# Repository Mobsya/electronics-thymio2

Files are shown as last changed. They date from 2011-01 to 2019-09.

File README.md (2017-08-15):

# electronics-thymio2

This is the official [Thymio II](www.thymio.org) electronis repository.
You will find here all files necessary to build and make the main PCB of Thymio II robots.
Source files are in Altium format but you can also found in /outbput common fabrication files. 

Thymio II is an open hardware robot, with its design freely available under a [Creative Commons Attribution-ShareAlike 3.0](https://creativecommons.org/licenses/by-sa/3.0/) license.

## Authors

The current version of the Thymio II robot, is an evolution of a first Thymio robot. 
Both were developed in the context of a collaboration between the [MOBOTS](http://mobots.epfl.ch/) group of the Swiss Federal Institute of Technology in Lausanne ([EPFL](www.epfl.ch)) and the Lausanne Arts School ([ECAL](http://www.ecal.ch)).
For Thymio II, the development was supported by the [NCCR](https://www.nccr-robotics.ch/) Robotics research program, while [Mobsya association](www.mobsya.org) took part in the development and manages the production.

Initial electronics version was made by:
* Dr Fanny Riedo
* Dr Michael Bonani
* Dr Philippe Rétornaz

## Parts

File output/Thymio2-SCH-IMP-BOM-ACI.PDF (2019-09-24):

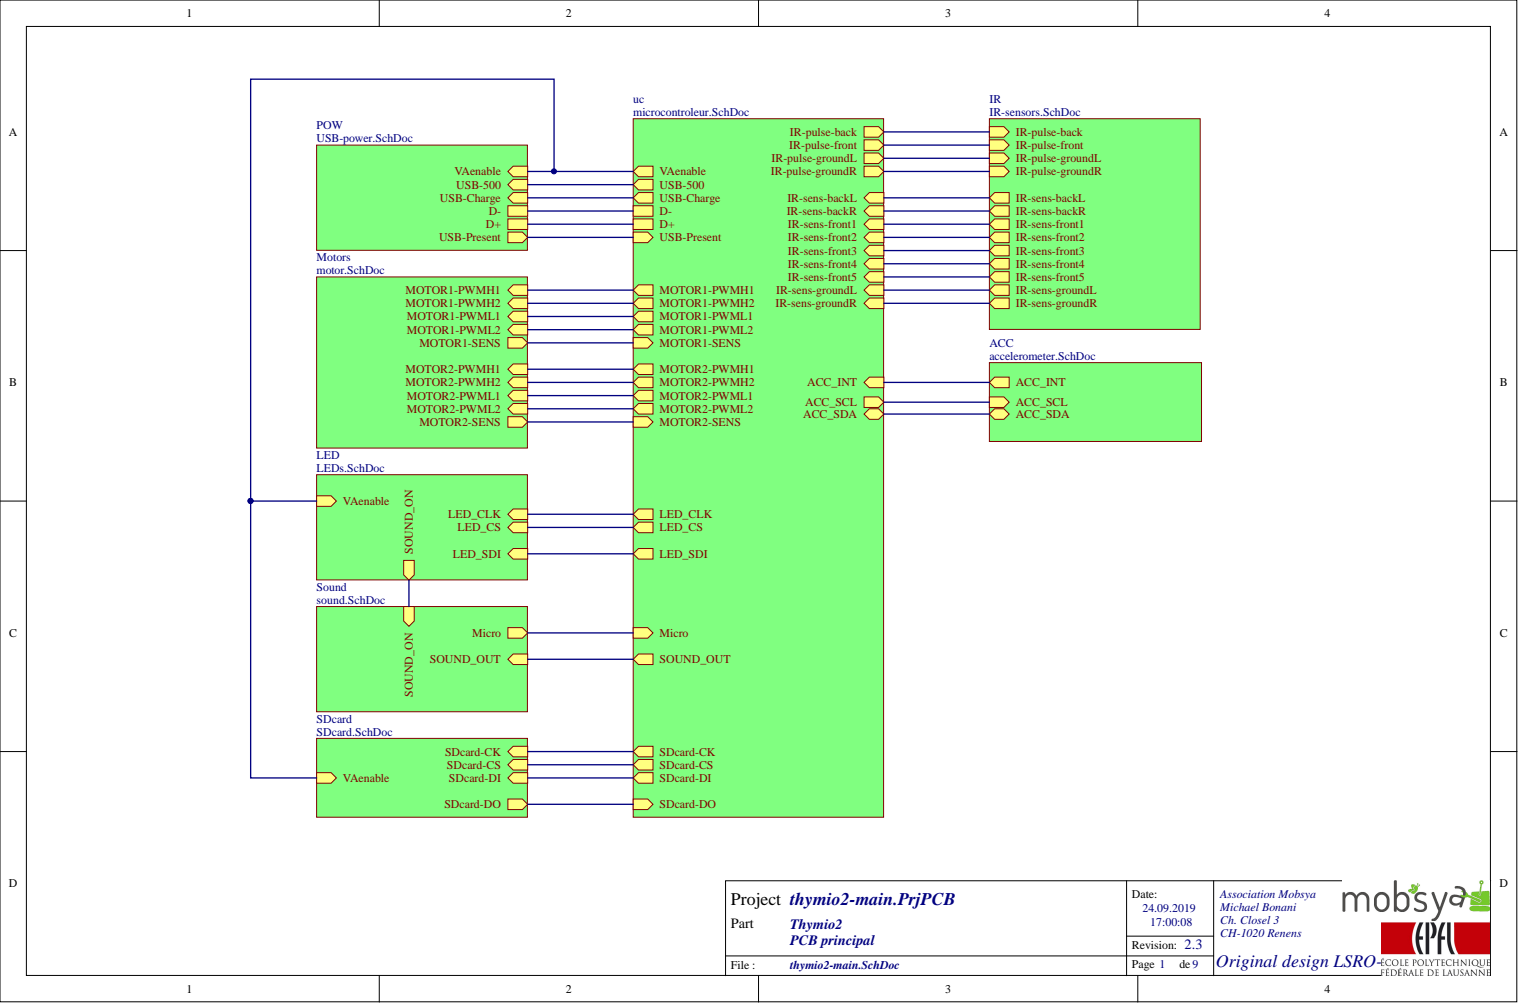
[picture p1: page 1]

S2 | | | | ENVREG 57 | PGC Buton2 2

VCAP/VDDCORE 56 | Buton3 3

Buton4 | | 4

VBUS 34 | | Buton5 | | 5
VUSB 35 | | | | 6

RT1 | USB-500 USB-Charge

R137 | PMA9/RP10/SDA2/CN17/RF4 31

MOTOR1-PWML1 | PMA8/RP17/SCL2/CN18/RF5 32 D-/RG3 36 D+/RG2 37

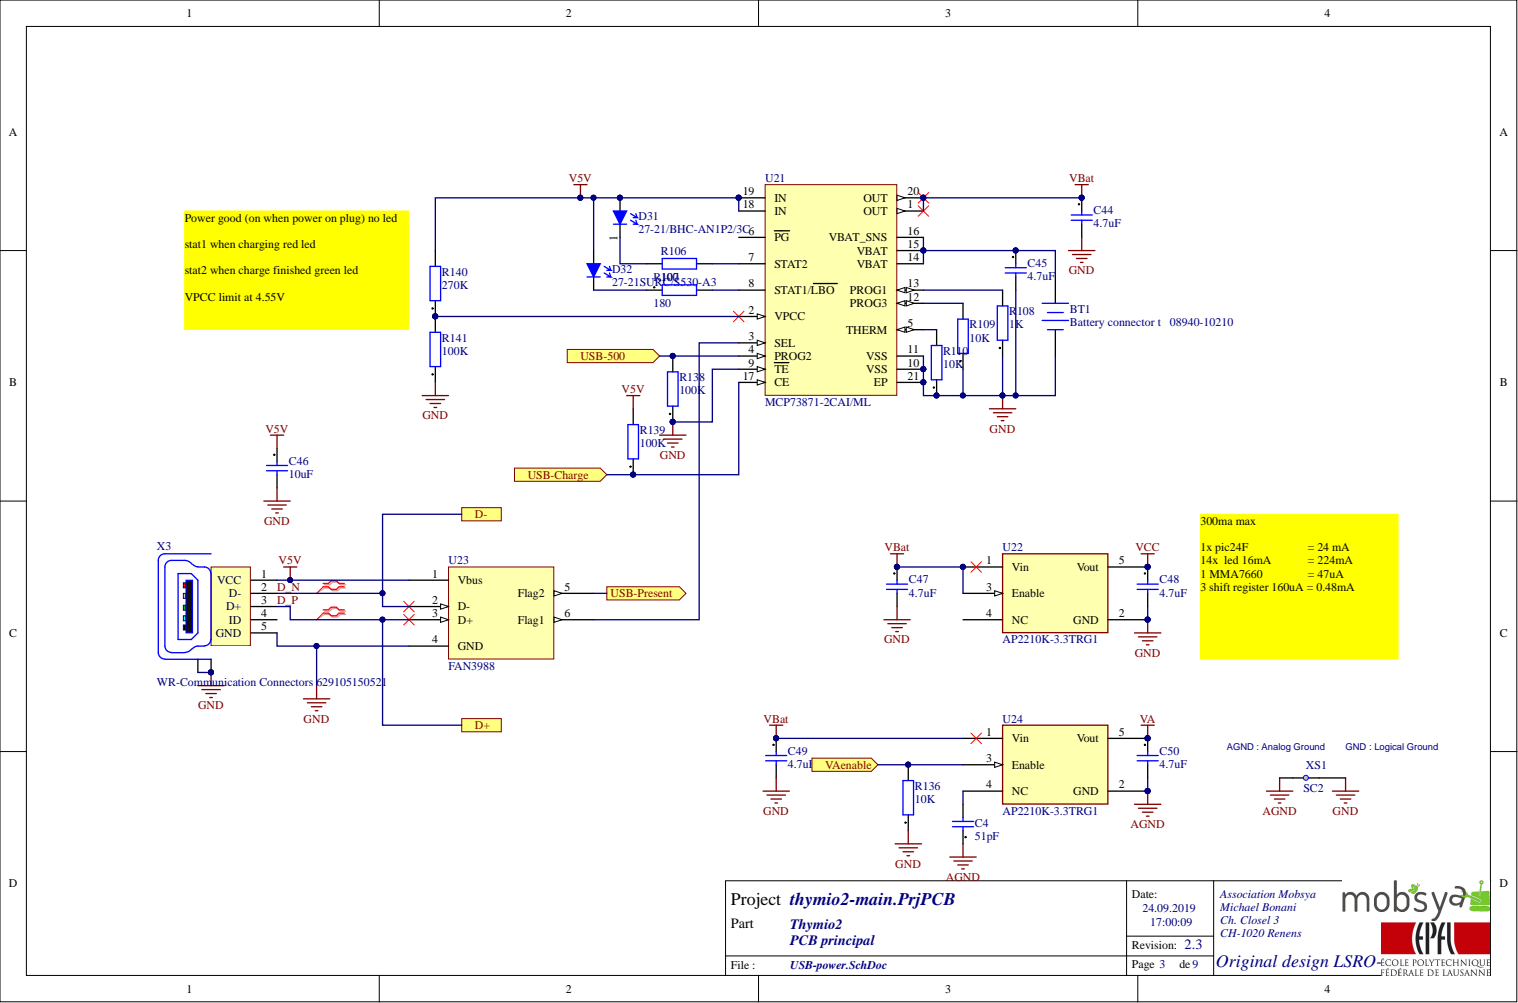
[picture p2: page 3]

Power good (on when power on plug) no led

stat1 when charging red led

stat2 when charge finished green led

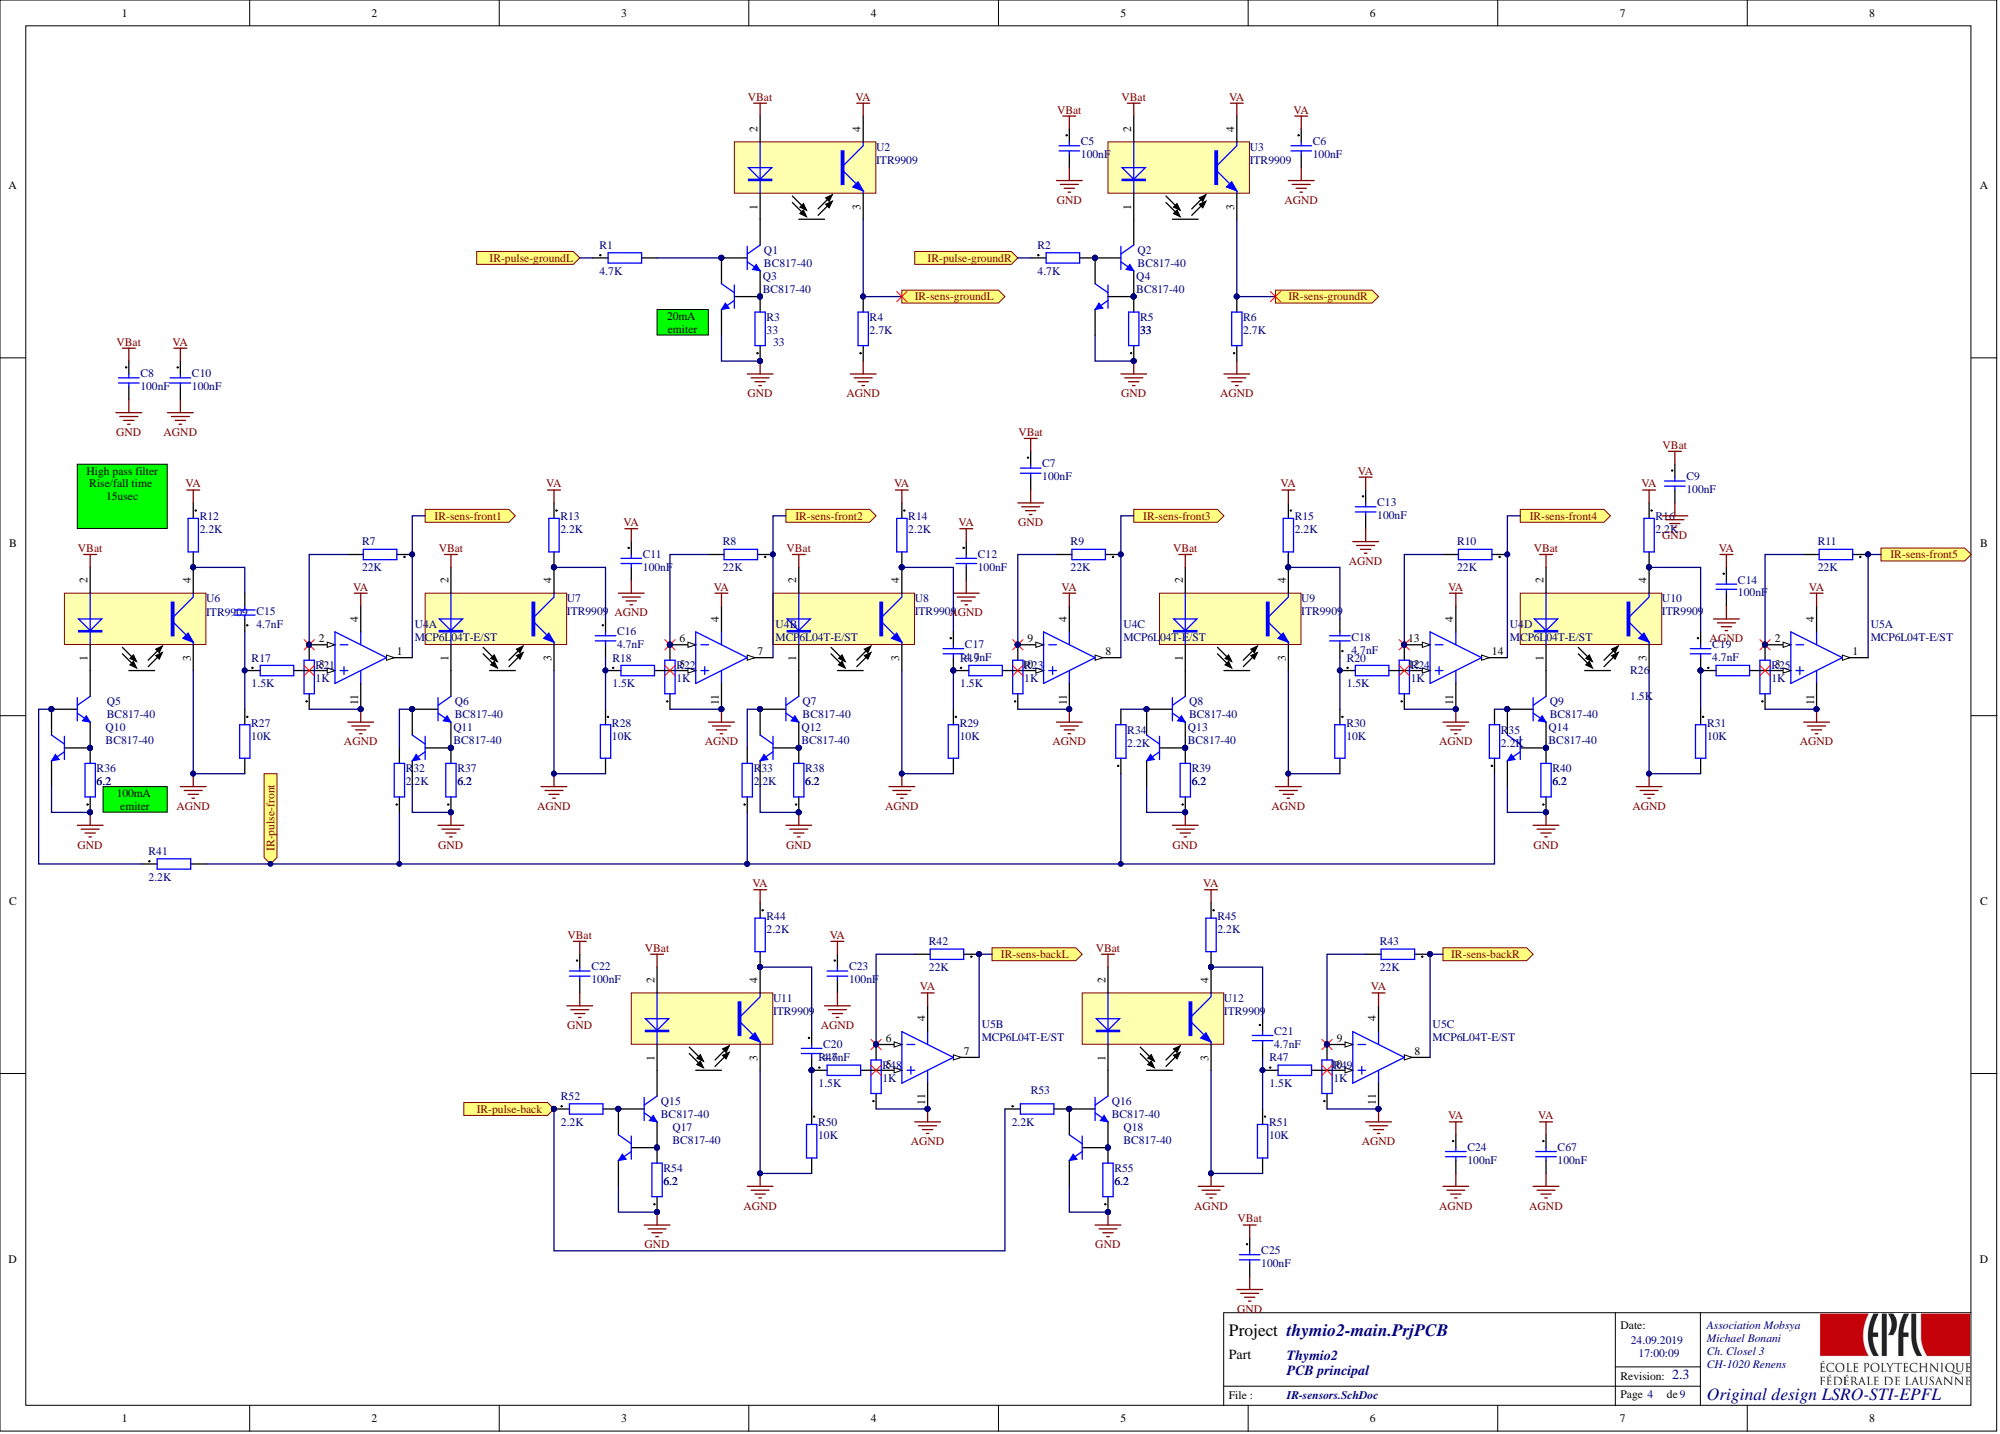
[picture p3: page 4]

100mA emiter

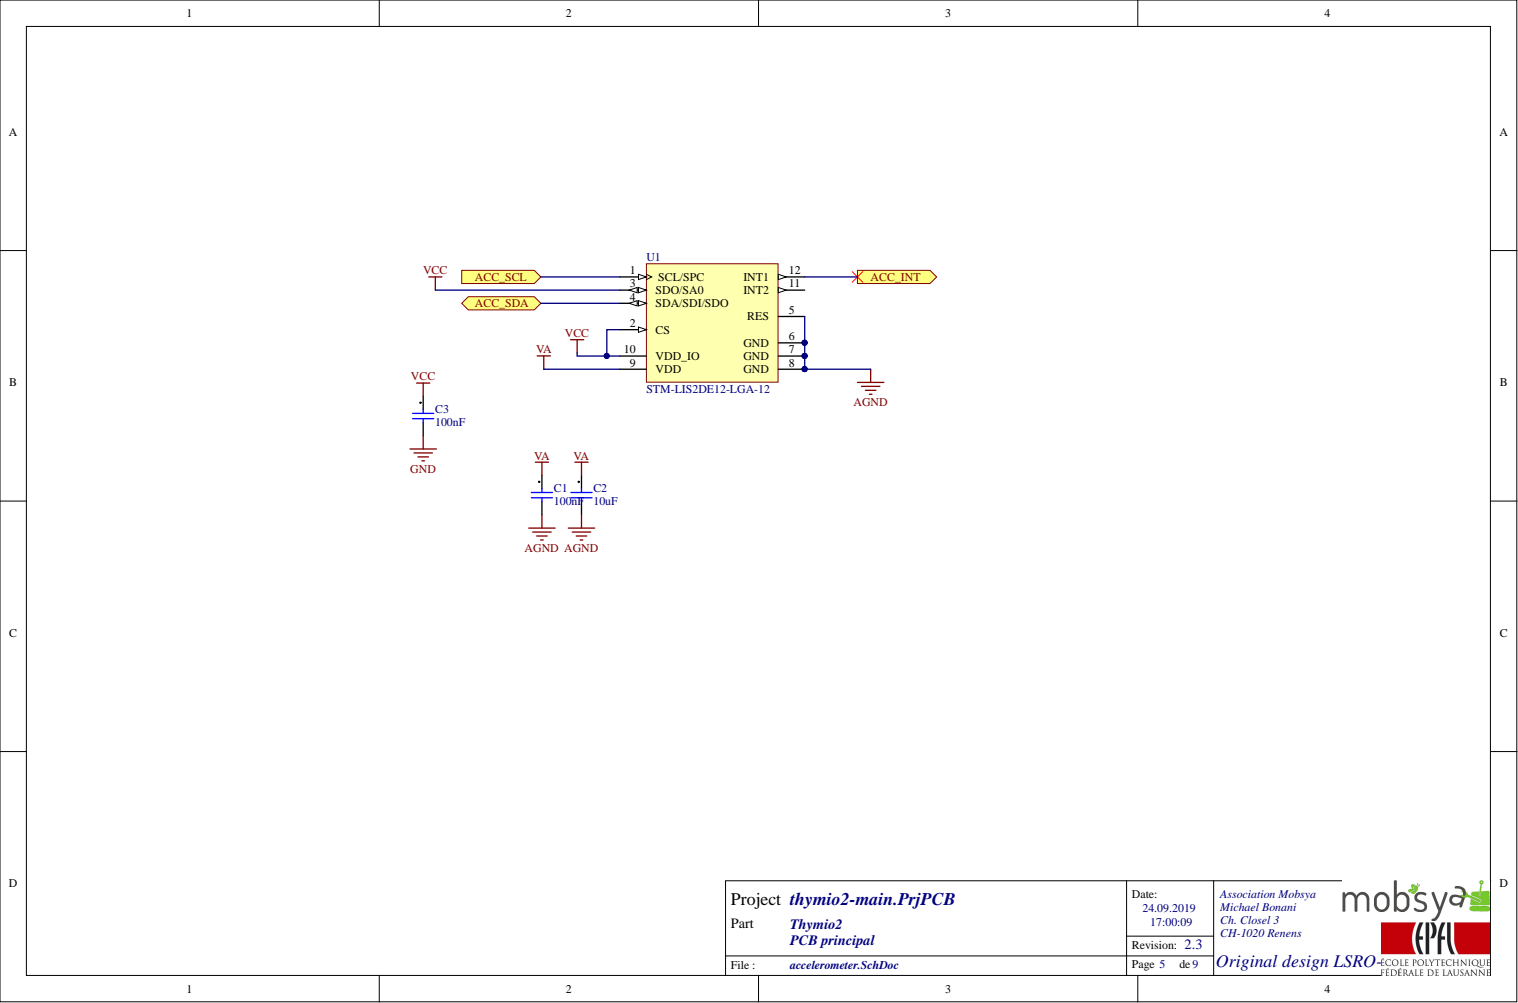
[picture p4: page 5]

2 side RGB bottom
red for SD card

4 red for interface button circle
2 led for interface circe

GND
6 front led red sensors

6 green for interface circle
1 red IR comunication D7
1 blue sound level D8

2 side led red sensors
1 RGB top all robot
3 side led green batery

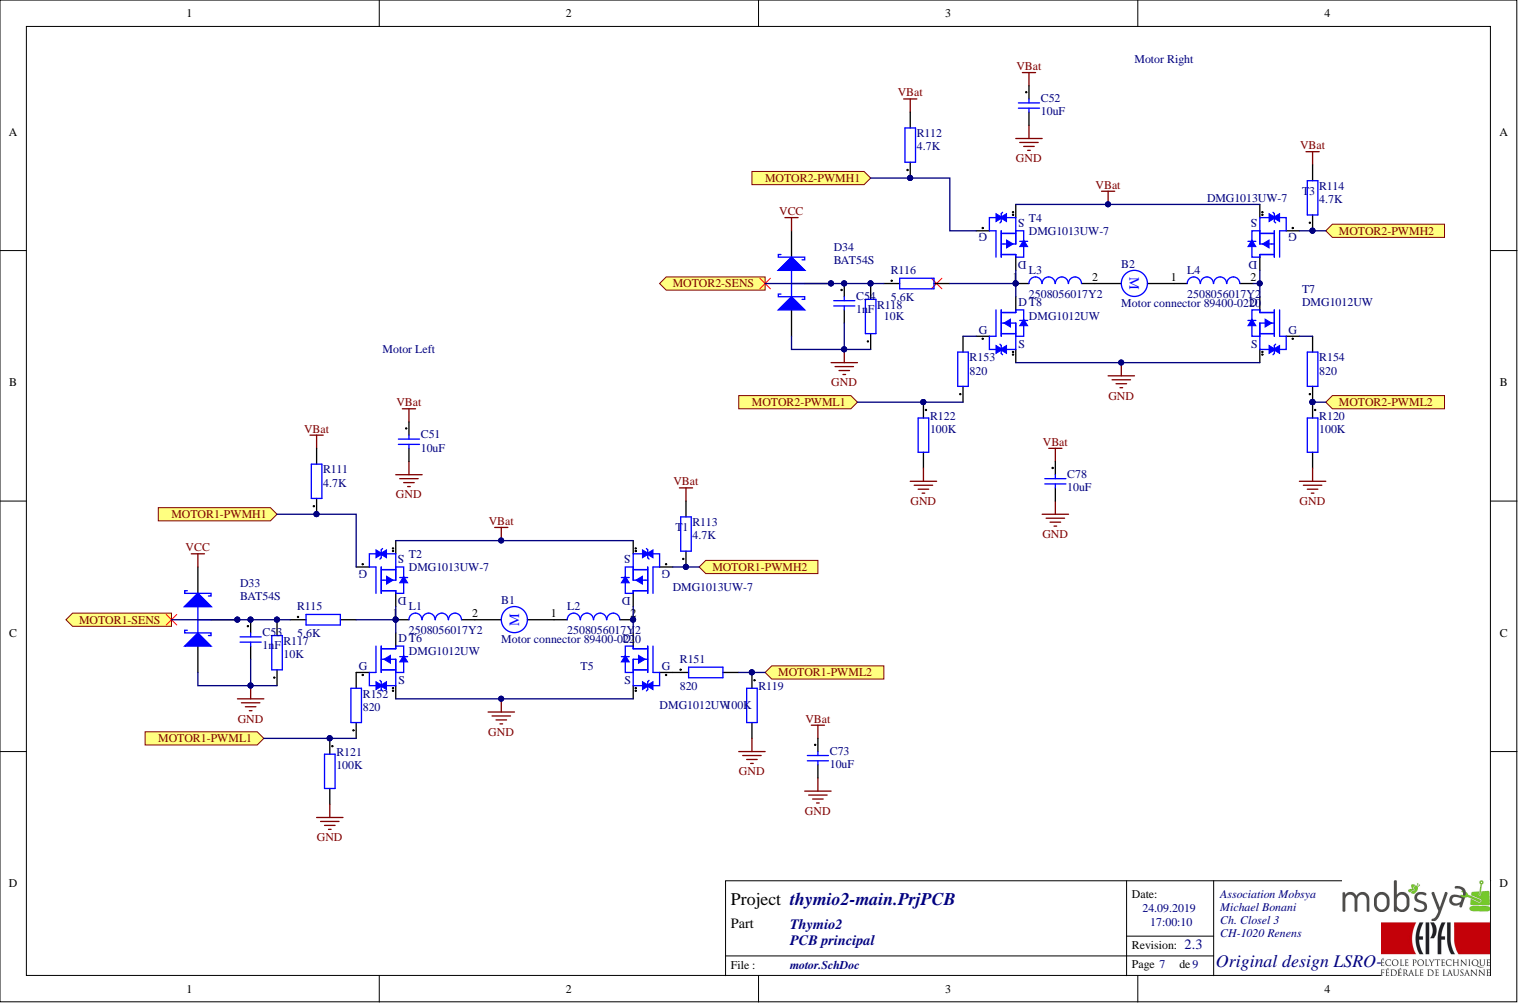
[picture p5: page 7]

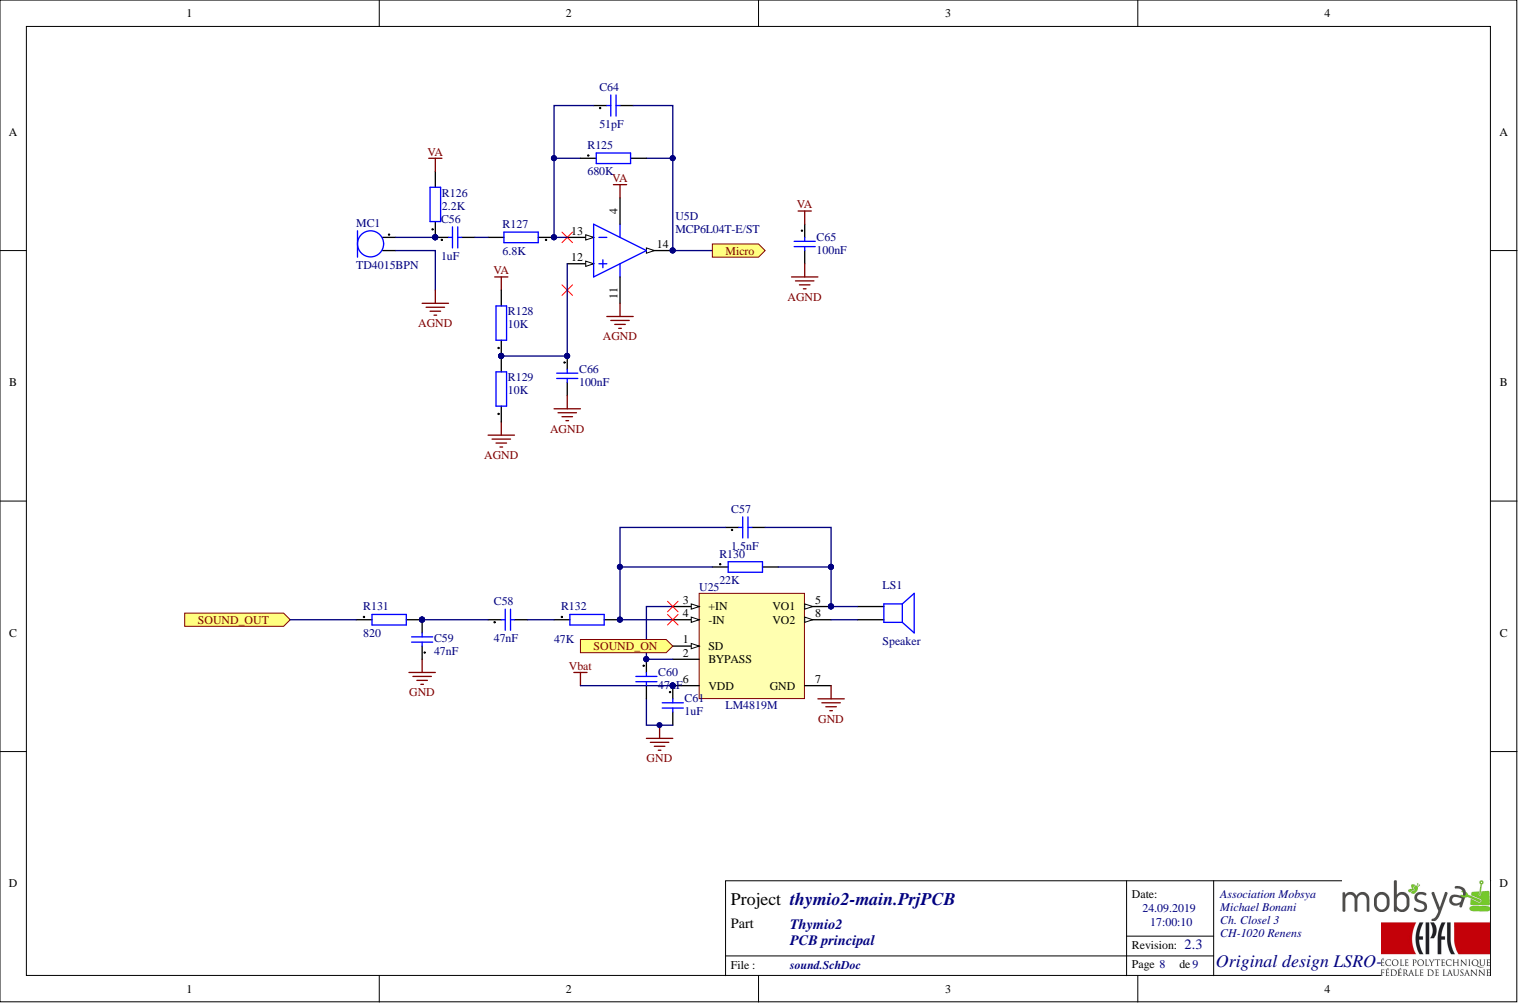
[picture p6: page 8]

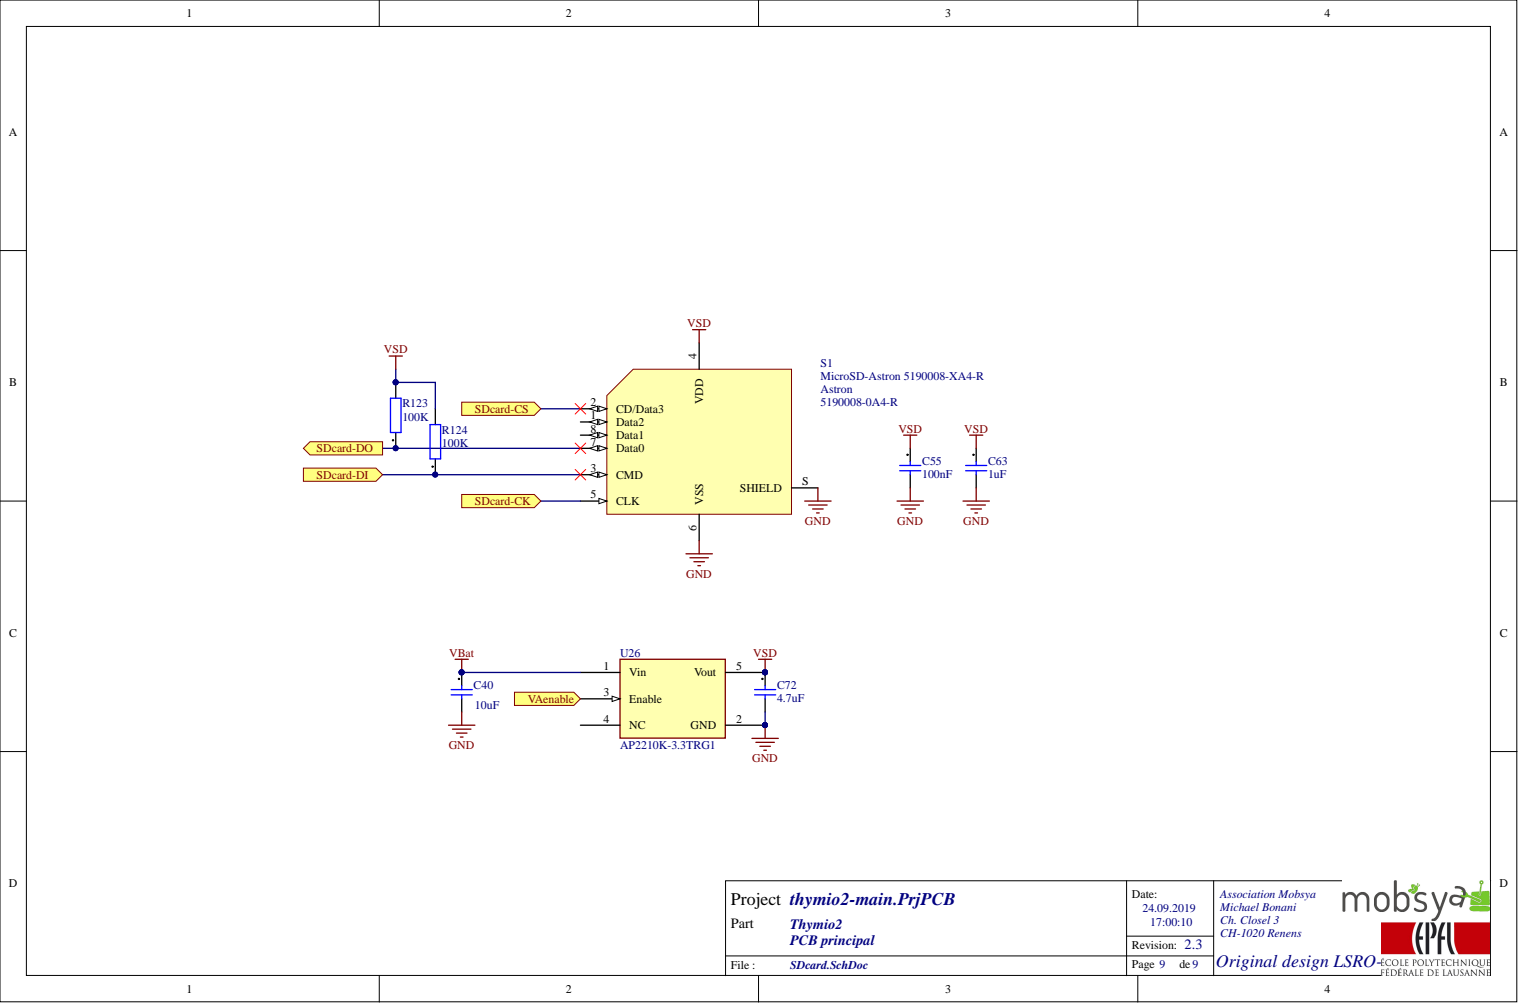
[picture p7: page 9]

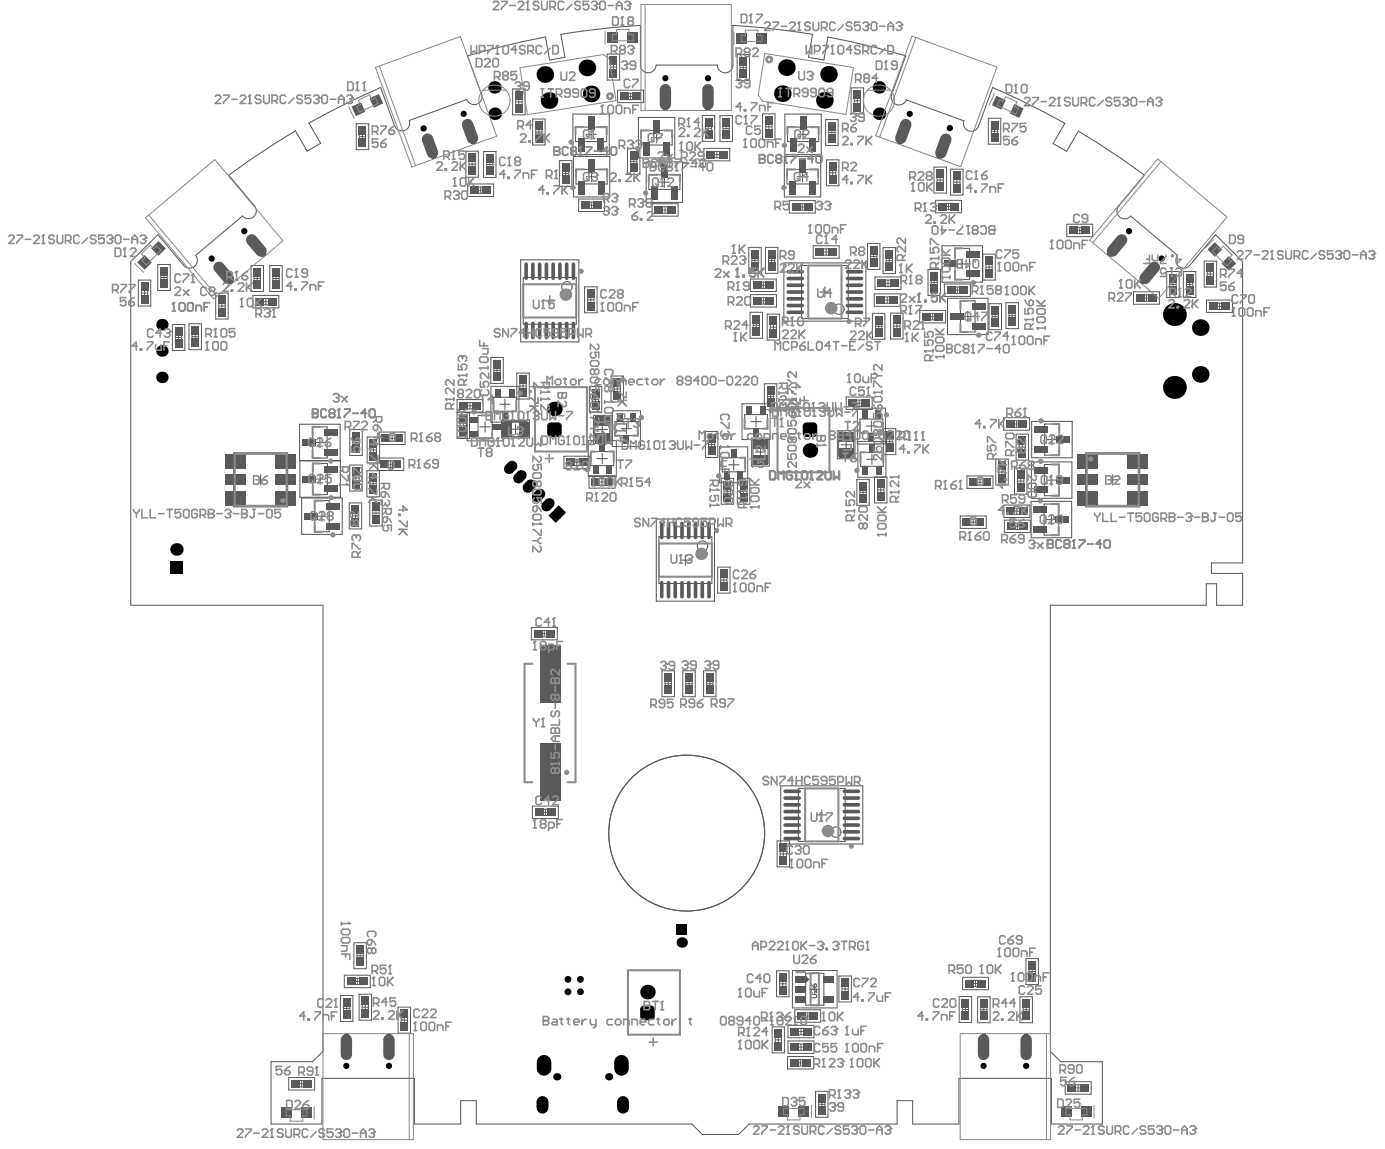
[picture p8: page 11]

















Quantity | Comment | Designator | Description | Footprint
2 | Motor connector 89400-022B1, B2 | | Motor, General Kind | BAT-2
1 | Battery connector t 08940BT1 | | Multicell Battery | BAT-2
38 | 100nF | C1, C3, C5, C6, C7, C8, C9, C10, C11, Cap acitor | | CAP C100 5X05N
8 | 10uF | C2, C31, C40, C46, C51, C52, C73, C78Capacitor | | CAPC1005X05N
2 | 51pF | C4, C64 | Capacitor | CAPC1005X05N
7 | 4.7nF | C15, C16, C17, C18, C19, C20, C21 | Capacitor | CAPC1005X05N
9 | 4.7uF | C32, C43, C44, C45, C47, C48, C49, C5Ca pacitor | | CAPC1005X05N
1 | 10uF X5R | C34 | Capacitor | CAPC1005X05N
2 | 18pF | C41, C42 | | CAPC1005X05N
2 | 1nF | C53, C54 | Capacitor | CAPC1005X05N
3 | 1uF | C56, C61, C63 | Capacitor | CAPC1005X05N
1 | 1.5nF | C57 | Capacitor | CAPC1005X05N
3 | 47nF | C58, C59, C60 | Capacitor | CAPC1005X05N
4 | 19-21SURC/S530-A3/TR8 | D1, D3, D4, D5 | SMD Red 0603 2V@20ma 56 mcd | DIOC1608X08N
4 | YLL-T50GRB-3-BJ-05 | D2, D6, D27, D38 | | QBLP679E-RGB
12 | 27-21SURC/S530-A3 | D7, D9, D10, D11, D12, D17, D18, D2S MDR edled righ tangle mount 2V@227-21EVERLIGHT
3 | 27-21/BHC-AN1P2/3C | D8, D31, D37 | SMD Blue led right angle mount 3.3 27- 1Everlight Blue
8 | APTD1608SYCK | D13, D14, D15, D16, D21, D22, D23, | DLED standard - CMS Helios SMD YeDIOC1608X08N
2 | WP7104SRC/D | D19, D20 | Red led 2V@20ma 57mcd | LED_TH_3MM_20MM
3 | APTD1608CGCK | D28, D29, D30 | LED standard - CMS Helios SMD GrDIOC1608X08N
2 | BAT54S | D33, D34 | Schottky Barrier Double Diode | SOT23_N
5 | 2508056017Y2 | L1, L2, L3, L4, L5 | SMD EMI Suppression Ferrite BeadINDC2012 X11L
1 | Speaker | LS1 | Loudspeaker | PIN2
1 | TD4015BPN | MC1 | Omnidirectional Back Electret CondMICRO_TD4015BPN
36 | BC817-40 | Q1, Q2, Q3, Q4, Q5, Q6, Q7, Q8, Q9, | NPN Gen eral-p urpo seTr ansisto r | S OT2 3_N
18 | 4.7K | R1, R2, R57, R59, R61, R63, R64, R65, Resis tor | | RES C1005 X04N
2 | 33 | R3, R5 | 120, Resistor | RESC1005X04N
2 | 2.7K | R4, R6 | Resistor | RESC1005X04N
10 | 22K | R7, R8, R9, R10, R11, R42, R43, R67, | R120, Resistor | RESC1005X04N
17 | 2.2K | R12, R13, R14, R15, R16, R32, R33, R312 0, Re sisto r | | RES C100 5X04N
7 | 1.5K | R17, R18, R19, R20, R26, R46, R47 | 120 | RESC1005X04N
10 | 1K | R21, R22, R23, R24, R25, R48, R49, R1120 , Resis tor | | RESC1005X04N
16 | 10K | R27, R28, R29, R30, R31, R50, R51, R1120 , Resis tor | | RESC 1005X 04N
7 | 6.2 | R36, R37, R38, R39, R40, R54, R55 | 120 | RESC1005X04N
18 | 56 | R56, R58, R60, R62, R69, R72, R74, R7Re sisto r, 56 | | RE SC1 005X0 4N
14 | 39 | R66, R82, R83, R84, R85, R86, R87, R8Re sisto r | | RESC1005X04N
4 | 200 | R68, R71, R98, R147 | 200 | RESC1005X04N
4 | 82 | R70, R73, R100, R149 | 82 | RESC1005X04N
4 | 100 | R105, R106, R135, R150 | Resistance, Resistor | RESC1005X04N
2 | 180 | R107, R137 | Resistor | RESC1005X04N
2 | 5.6K | R115, R116 | Resistor | RESC1005X04N
15 | 100K | R119, R120, R121, R122, R123, R124, | Resis tor | R ESC1 005X0 4N
1 | 680K | R125 | Resistor | RESC1005X04N
1 | 6.8K | R127 | Resistor | RESC1005X04N
5 | 820 | R131, R151, R152, R153, R154 | Resistor | RESC1005X04N
1 | 47K | R132 | Resistor | RESC1005X04N
1 | 270K | R140 | Resistor | RESC1005X04N
6 | 0 | R160, R161, R168, R169, R170, R171 | Resistor | RESC1005X04N
1 | NCP15XH103F03RC | RT1 | Thermistors - NTC 10K OHM 1% 04RESC1005X04L
1 | MicroSD-Astron 5190008-XA4S1 | | MicroSD Card connector 5190008-XAstron 5190008-XA4-R
1 | SW-PB | S2 | Switch | FSMRA2JH
4 | DMG1013UW-7 | T1, T2, T3, T4 | Transistor MOSFET 1 x P Pining : 1=SO T65P 210X100-3N
4 | DMG1012UW | T5, T6, T7, T8 | Transistor MOSFET 1 x N, Pining : 1SOT 65P2 10X100-3N
1 | STM-LIS2DE12-LGA-12 | U1 | | STM-LGA-12
2 | ITR9909 | U2, U3 | Everlight Opto Interrupter | ITR9909_LONG
2 | MCP6L04T-E/ST | U4, U5 | 1MHz, 85 µA Quad Op Amp, 14-PinTSSOP-S T14_N
7 | ITR9909 | U6, U7, U8, U9, U10, U11, U12 | Everlight Opto Interrupter | ITR9909_EDGE
5 | SN74HC595PWR | U13, U14, U15, U16, U17 | 8-Bit Serial-Input/Serial or Prallel-O948F-01_N
1 | AP2112K-3.3TRG1 | U18 | 300mA, Low Quiescent Current, FaSOT95P285X100-5N
1 | PIC24FJ128GB106-I/PT | U19 | General Purpose 16-Bit Flash MicroTQFP-PT64_N
1 | IRM-3638T | U20 | IR Receiver Module (38 kHz) for ReIR-receiver
1 | MCP73871-2CAI/ML | U21 | Stand-Alone System Load Sharing QFN-ML20_N
3 | AP2210K-3.3TRG1 | U22, U24, U26 | 300mA, Low Quiescent Current, FaSOT95P285X100-5N
1 | FAN3988 | U23 | USB/Charger and Over Voltage DeMLP1.45X1MM
1 | LM4819M | U25 | 350mW Audio Power Amplifier withM08A_N
1 | Con1x6 | X2 | 1 x 6 pins connector | MHDR1X6
1 | WR-Communication ConneX3 | | WR-COM_USB_Micro Type B_Hor629105150521
1 | 815-ABLS-8-B2 | Y1 | Surface Mount Quartz Crystal 8MhzHC49/4H_SMX

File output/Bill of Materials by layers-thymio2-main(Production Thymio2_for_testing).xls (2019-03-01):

Quantity | Comment | Designator | Description | Footprint | Layer
1 | 1uF | C63 | Capacitor | CAPC1005X05N | Bottom
1 | 6.2 | R38 | 120 | RESC1005X04N | Bottom
1 | 100 | R105 | Resistance | RESC1005X04N | Bottom
1 | 815-ABLS-8-B2 | Y1 | Surface Mount Quartz Crystal 8Mhz | HC49/4H_SMX | Bottom
1 | AP2210K-3.3TRG1 | U26 | 300mA, Low Quiescent Current, Fast Transient LDO | SOT95P285X100-5N | Bottom
1 | Battery connector t 08940-10210 | BT1 | Multicell Battery | BAT-2 | Bottom
1 | MCP6L04T-E/ST | U4 | 1 MHz, 85 µA Quad Op Amp, 14-Pin TSSOP, Extended Temperature Range, Tape and Reel | TSSOP-ST14_N | Bottom
2 | 2.7K | R4, R6 | Resistor | RESC1005X04N | Bottom
2 | 4.7uF | C43, C72 | Capacitor | CAPC1005X05N | Bottom
2 | 18pF | C41, C42 |  | CAPC1005X05N | Bottom
2 | 33 | R3, R5 | 120, Resistor | RESC1005X04N | Bottom
2 | 82 | R70, R73 | 82 | RESC1005X04N | Bottom
2 | 200 | R68, R71 | 200 | RESC1005X04N | Bottom
2 | ITR9909 | U2, U3 | Everlight Opto Interrupter | ITR9909_LONG | Bottom
2 | Motor connector 89400-0220 | B1, B2 | Motor, General Kind | BAT-2 | Bottom
2 | WP7104SRC/D | D19, D20 | Red led 2V@20ma 57mcd | LED_TH_3MM_20MM | Bottom
2 | YLL-T50GRB-3-BJ-05 | D2, D6 |  | QBLP679E-RGB | Bottom
3 | SN74HC595PWR | U13, U15, U17 | 8-Bit Serial-Input/Serial or Prallel-Output Shift Register with Latched 3-State Outputs | 948F-01_N | Bottom
4 | 0 | R160, R161, R168, R169 | Resistor | RESC1005X04N | Bottom
4 | 1K | R21, R22, R23, R24 | 120 | RESC1005X04N | Bottom
4 | 1.5K | R17, R18, R19, R20 | 120 | RESC1005X04N | Bottom
4 | 22K | R7, R8, R9, R10 | 120 | RESC1005X04N | Bottom
4 | 820 | R151, R152, R153, R154 | Resistor | RESC1005X04N | Bottom
4 | 2508056017Y2 | L1, L2, L3, L4 | SMD EMI Suppression Ferrite Bead WE-CBF, Z = 600 Ohm | INDC2012X11L | Bottom
4 | DMG1012UW | T5, T6, T7, T8 | Transistor MOSFET 1 x N, Pining : 1=G, 2=S, 3=D | SOT65P210X100-3N | Bottom
4 | DMG1013UW-7 | T1, T2, T3, T4 | Transistor MOSFET 1 x P Pining : 1=G, 2=S, 3=D | SOT65P210X100-3N | Bottom
5 | 10uF | C40, C51, C52, C73, C78 | Capacitor | CAPC1005X05N | Bottom
7 | 4.7nF | C15, C16, C17, C18, C19, C20, C21 | Capacitor | CAPC1005X05N | Bottom
8 | 2.2K | R12, R13, R14, R15, R16, R33, R44, R45 | 120, Resistor | RESC1005X04N | Bottom
8 | 10K | R27, R28, R29, R30, R31, R50, R51, R136 | 120, Resistor | RESC1005X04N | Bottom
8 | 39 | R82, R83, R84, R85, R95, R96, R97, R133 | Resistor | RESC1005X04N | Bottom
8 | 56 | R69, R72, R74, R75, R76, R77, R90, R91 | 56, Resistor | RESC1005X04N | Bottom
9 | 27-21SURC/S530-A3 | D9, D10, D11, D12, D17, D18, D25, D26, D35 | SMD Red led right angle mount 2V@20ma 57mcd | 27-21 EVERLIGHT | Bottom
10 | 100K | R119, R120, R121, R122, R123, R124, R155, R156, R157, R158 | Resistor | RESC1005X04N | Bottom
12 | 4.7K | R1, R2, R57, R59, R61, R63, R64, R65, R111, R112, R113, R114 | Resistor | RESC1005X04N | Bottom
14 | BC817-40 | Q1, Q2, Q3, Q4, Q7, Q12, Q19, Q20, Q22, Q25, Q26, Q28, Q47, Q48 | NPN General-purpose Transistor | SOT23_N | Bottom
17 | 100nF | C5, C7, C8, C9, C14, C22, C25, C26, C28, C30, C55, C68, C69, C70, C71, C74, C75 | Capacitor | CAPC1005X05N | Bottom
1 | 1.5nF | C57 | Capacitor | CAPC1005X05N | Top
1 | 6.8K | R127 | Resistor | RESC1005X04N | Top
1 | 10uF X5R | C34 | Capacitor | CAPC1005X05N | Top
1 | 47K | R132 | Resistor | RESC1005X04N | Top
1 | 270K | R140 | Resistor | RESC1005X04N | Top
1 | 680K | R125 | Resistor | RESC1005X04N | Top
1 | 820 | R131 | Resistor | RESC1005X04N | Top
1 | 2508056017Y2 | L5 | SMD EMI Suppression Ferrite Bead WE-CBF, Z = 600 Ohm | INDC2012X11L | Top
1 | AP2112K-3.3TRG1 | U18 | 300mA, Low Quiescent Current, Fast Transient LDO | SOT95P285X100-5N | Top
1 | Con1x6 | X2 | 1 x 6 pins connector | MHDR1X6 | Top
1 | FAN3988 | U23 | USB/Charger and Over Voltage Detection Device | MLP 1.45X1MM | Top
1 | IRM-3638T | U20 | IR Receiver Module (38 kHz) for Remote Control Systems | IR-receiver | Top
1 | LM4819M | U25 | 350mW Audio Power Amplifier with Shutdown Mode | M08A_N | Top
1 | MCP6L04T-E/ST | U5 | 1 MHz, 85 µA Quad Op Amp, 14-Pin TSSOP, Extended Temperature Range, Tape and Reel | TSSOP-ST14_N | Top
1 | MCP73871-2CAI/ML | U21 | Stand-Alone System Load Sharing and Li-Ion/Li-Polymer Battery Charge Management Controller, 4.2V, 20-Pin QFN, Industrial Temperature | QFN-ML20_N | Top
1 | MicroSD-Astron 5190008-XA4-R | S1 | MicroSD Card connector 5190008-XA4-R | Astron 5190008-XA4-R | Top
1 | NCP15XH103F03RC | RT1 | Thermistors - NTC 10K OHM 1% 0402 | RESC1005X04L | Top
1 | PIC24FJ128GB106-I/PT | U19 | General Purpose 16-Bit Flash Microcontroller with USB On-The-Go, 128KB Flash, 16KB SRAM, 64-Pin TQFP, Industrial Temperature | TQFP-PT64_N | Top
1 | Speaker | LS1 | Loudspeaker | PIN2 | Top
1 | STM-LIS2DE12-LGA-12 | U1 |  | STM-LGA-12 | Top
1 | SW-PB | S2 | Switch | FSMRA2JH | Top
1 | TD4015BPN | MC1 | Omnidirectional Back Electret Condenser Microphone | MICRO_TD4015BPN | Top
1 | WR-Communication Connectors 629105150521 | X3 | WR-COM_USB_Micro Type B_Horizontal_SMT | 629105150521 | Top
2 | 0 | R172, R173 | Resistor | RESC1005X04N | Top
2 | 1nF | C53, C54 | Capacitor | CAPC1005X05N | Top
2 | 1uF | C56, C61 | Capacitor | CAPC1005X05N | Top
2 | 5.6K | R115, R116 | Resistor | RESC1005X04N | Top
2 | 51pF | C4, C64 | Capacitor | CAPC1005X05N | Top
2 | 82 | R100, R149 | 82 | RESC1005X04N | Top
2 | 180 | R107, R137 | Resistor | RESC1005X04N | Top
2 | 200 | R99, R148 | 200 | RESC1005X04N | Top
2 | AP2210K-3.3TRG1 | U22, U24 | 300mA, Low Quiescent Current, Fast Transient LDO | SOT95P285X100-5N | Top
2 | BAT54S | D33, D34 | Schottky Barrier Double Diode | SOT23_N | Top
2 | QBLP679E-RGB | D27, D38 |  | QBLP679E-RGB | Top
2 | SN74HC595PWR | U14, U16 | 8-Bit Serial-Input/Serial or Prallel-Output Shift Register with Latched 3-State Outputs | 948F-01_N | Top
3 | 1.5K | R26, R46, R47 | 120 | RESC1005X04N | Top
3 | 10uF | C2, C31, C46 | Capacitor | CAPC1005X05N | Top
3 | 27-21/BHC-AN1P2/3C | D8, D31, D37 | SMD Blue led right angle mount 3.3V@20ma 28mcd | 27-21 Everlight Blue | Top
3 | 27-21SURC/S530-A3 | D7, D32, D36 | SMD Red led right angle mount 2V@20ma 57mcd | 27-21 EVERLIGHT | Top
3 | 47nF | C58, C59, C60 | Capacitor | CAPC1005X05N | Top
3 | 100 | R106, R135, R150 | Resistance, Resistor | RESC1005X04N | Top
3 | APTD1608CGCK | D28, D29, D30 | LED standard - CMS Helios SMD Green 570nm 230mcd | DIOC1608X08N | Top
4 | 19-21SURC/S530-A3/TR8 | D1, D3, D4, D5 | SMD Red 0603 2V@20ma 56 mcd | DIOC1608X08N | Top
5 | 100K | R138, R139, R141, R143, R159 | Resistor | RESC1005X04N | Top
6 | 1K | R25, R48, R49, R108, R166, R167 | 120, Resistor | RESC1005X04N | Top
6 | 4.7K | R92, R93, R94, R144, R145, R146 | Resistor | RESC1005X04N | Top
6 | 6.2 | R36, R37, R39, R40, R54, R55 | 120 | RESC1005X04N | Top
6 | 22K | R11, R42, R43, R67, R130, R142 | 120, Resistor | RESC1005X04N | Top
6 | 39 | R66, R86, R87, R88, R89, R134 | Resistor | RESC1005X04N | Top
7 | 4.7uF | C32, C44, C45, C47, C48, C49, C50 | Capacitor | CAPC1005X05N | Top
7 | ITR9909 | U6, U7, U8, U9, U10, U11, U12 | Everlight Opto Interrupter | ITR9909_EDGE | Top
8 | 10K | R101, R102, R109, R110, R117, R118, R128, R129 | Resistor | RESC1005X04N | Top
8 | APTD1608SYCK | D13, D14, D15, D16, D21, D22, D23, D24 | LED standard - CMS Helios SMD Yellow 590nm 480mcd | DIOC1608X08N | Top
9 | 2.2K | R32, R34, R35, R41, R52, R53, R103, R104, R126 | Resistor | RESC1005X04N | Top
10 | 56 | R56, R58, R60, R62, R78, R79, R80, R81, R98, R147 | Resistor, 56 | RESC1005X04N | Top
21 | 100nF | C1, C3, C6, C10, C11, C12, C13, C23, C24, C27, C29, C33, C35, C36, C37, C38, C39, C62, C65, C66, C67 | Capacitor | CAPC1005X05N | Top
22 | BC817-40 | Q5, Q6, Q8, Q9, Q10, Q11, Q13, Q14, Q15, Q16, Q17, Q18, Q31, Q32, Q34, Q37, Q38, Q39, Q40, Q42, Q45, Q46 | NPN General-purpose Transistor | SOT23_N | Top

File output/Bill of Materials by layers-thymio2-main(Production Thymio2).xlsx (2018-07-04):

Quantity | Comment | Designator | Description | Footprint | Layer
1 | 100 | R105 | Resistance | RESC1608X06N | Bottom
1 | 1uF | C63 | Capacitor | CAPC1608X08L | Bottom
1 | 6.2 | R38 | 120 | RESC1608X06L | Bottom
1 | 815-ABLS-8-B2 | Y1 | Surface Mount Quartz Crystal 8Mhz | HC49/4H_SMX | Bottom
1 | AP7331-33WG-7 | U26 | 300mA, Low Quiescent Current, Fast Transient LDO | SOT95P285X100-5N | Bottom
1 | Battery connector t 08940-10210 | BT1 | Multicell Battery | BAT-2 | Bottom
1 | MCP6L04T-E/ST | U4 | 1 MHz, 85 µA Quad Op Amp, 14-Pin TSSOP, Extended Temperature Range, Tape and Reel | TSSOP-ST14_N | Bottom
10 | 100K | R119, R120, R121, R122, R123, R124, R155, R156, R157, R158 | Resistor | RESC1608X06L | Bottom
12 | 4.7K | R1, R2, R57, R59, R61, R63, R64, R65, R111, R112, R113, R114 | Resistor | RESC1608X06L | Bottom
14 | BC817-40 | Q1, Q2, Q3, Q4, Q7, Q12, Q19, Q20, Q22, Q25, Q26, Q28, Q47, Q48 | NPN General-purpose Transistor | SOT23_N | Bottom
17 | 100nF | C5, C7, C8, C9, C14, C22, C25, C26, C28, C30, C55, C68, C69, C70, C71, C74, C75 | Capacitor | CAPC1608X08L | Bottom
2 | 18pF | C41, C42 |  | CAPC1608X08L | Bottom
2 | 2.7K | R4, R6 | Resistor | RESC1608X06L | Bottom
2 | 200 | R69, R72 | 200 | RESC1608X06L | Bottom
2 | 33 | R3, R5 | 120, Resistor | RESC1608X06L | Bottom
2 | 4.7uF | C43, C72 | Capacitor | CAPC1608X08L | Bottom
2 | 82 | R70, R73 | 82 | RESC1608X06L | Bottom
2 | ITR9909 | U2, U3 | Everlight Opto Interrupter | ITR9909_LONG | Bottom
2 | Motor connector 89400-0220 | B1, B2 | Motor, General Kind | BAT-2 | Bottom
2 | QBLP679E-RGB | D2, D6 |  | QBLP679E-RGB | Bottom
2 | WP7104SRC/D | D19, D20 | Red led 2V@20ma 57mcd | LED_TH_3MM_20MM | Bottom
3 | SN74HC595PWR | U13, U15, U17 | 8-Bit Serial-Input/Serial or Prallel-Output Shift Register with Latched 3-State Outputs | 948F-01_N | Bottom
4 | 1.5K | R17, R18, R19, R20 | 120 | RESC1608X06L | Bottom
4 | 1K | R21, R22, R23, R24 | 120 | RESC1608X06L | Bottom
4 | 22K | R7, R8, R9, R10 | 120 | RESC1608X06L | Bottom
4 | 2508056017Y2 | L1, L2, L3, L4 | SMD EMI Suppression Ferrite Bead WE-CBF, Z = 600 Ohm | INDC2012X11L | Bottom
4 | 820 | R151, R152, R153, R154 | Resistor | RESC1608X06L | Bottom
4 | DMG1012T | T5, T6, T7, T8 | Transistor MOSFET 1 x N, Pining : 1=G, 2=S, 3=D | SOT50P160X80-3N | Bottom
4 | DMP21DOUT-7 | T1, T2, T3, T4 | Transistor MOSFET 1 x P Pining : 1=G, 2=S, 3=D | SOT50P160X80-3N | Bottom
5 | 10uF | C40, C51, C52, C73, C78 | Capacitor | CAPC1608X08L | Bottom
7 | 4.7nF | C15, C16, C17, C18, C19, C20, C21 | Capacitor | CAPC1608X08L | Bottom
8 | 10K | R27, R28, R29, R30, R31, R50, R51, R136 | 120, 120, 120, 120, 120, 120, 120, Resistor | RESC1608X06L | Bottom
8 | 2.2K | R12, R13, R14, R15, R16, R33, R44, R45 | 120, 120, 120, 120, 120, Resistor, 120, 120 | RESC1608X06L | Bottom
8 | 39 | R82, R83, R84, R85, R95, R96, R97, R133 | Resistor | RESC1608X06L | Bottom
8 | 56 | R68, R71, R74, R75, R76, R77, R90, R91 | 56, 56, Resistor, Resistor, Resistor, Resistor, Resistor, Resistor | RESC1608X06L | Bottom
9 | 27-21SURC/S530-A3 | D9, D10, D11, D12, D17, D18, D25, D26, D35 | SMD Red led right angle mount 2V@20ma 57mcd | 27-21 EVERLIGHT | Bottom
1 | 1.5nF | C57 | Capacitor | CAPC1608X08L | Top
1 | 100 | R106 | Resistance | RESC1608X06N | Top
1 | 10uF X5R | C34 | Capacitor | CAPC1608X08L | Top
1 | 2508056017Y2 | L5 | SMD EMI Suppression Ferrite Bead WE-CBF, Z = 600 Ohm | INDC2012X11L | Top
1 | 270K | R140 | Resistor | RESC1608X06L | Top
1 | 47K | R132 | Resistor | RESC1608X06L | Top
1 | 51pF | C64 | Capacitor | CAPC1608X08L | Top
1 | 6.8K | R127 | Resistor | RESC1608X06L | Top
1 | 680K | R125 | Resistor | RESC1608X06L | Top
1 | 820 | R131 | Resistor | RESC1608X06L | Top
1 | Con1x6 | X2 | 1 x 6 pins connector | MHDR1X6 | Top
1 | FAN3988 | U23 | USB/Charger and Over Voltage Detection Device | MLP 1.45X1MM | Top
1 | IRM-3638T | U20 | IR Receiver Module (38 kHz) for Remote Control Systems | IR-receiver | Top
1 | LM4819M | U25 | 350mW Audio Power Amplifier with Shutdown Mode | M08A_N | Top
1 | MCP6L04T-E/ST | U5 | 1 MHz, 85 µA Quad Op Amp, 14-Pin TSSOP, Extended Temperature Range, Tape and Reel | TSSOP-ST14_N | Top
1 | MCP73871-2CAI/ML | U21 | Stand-Alone System Load Sharing and Li-Ion/Li-Polymer Battery Charge Management Controller, 4.2V, 20-Pin QFN, Industrial Temperature | QFN-ML20_N | Top
1 | MicroSD-Astron 5190008-XA4-R | S1 | MicroSD Card connector 5190008-XA4-R | Astron 5190008-XA4-R | Top
1 | MMA7660FC | U1 | MMA7660FC: XYZ-AXIS ACCELEROMETER ±1.5 g | DFN50P300X300X100-12N | Top
1 | NCP15XH103F03RC | RT1 | Thermistors - NTC 10K OHM 1% 0402 | RESC1005X04L | Top
1 | PIC24FJ128GB106-I/PT | U19 | General Purpose 16-Bit Flash Microcontroller with USB On-The-Go, 128KB Flash, 16KB SRAM, 64-Pin TQFP, Industrial Temperature | TQFP-PT64_N | Top
1 | Speaker | LS1 | Loudspeaker | PIN2 | Top
1 | SW-PB | S2 | Switch | FSMRA2JH | Top
1 | TD4015BPN | MC1 | Omnidirectional Back Electret Condenser Microphone | MICRO_TD4015BPN | Top
1 | WR-Communication Connectors 629105150521 | X3 | WR-COM_USB_Micro Type B_Horizontal_SMT | 629105150521 | Top
10 | 56 | R56, R58, R60, R62, R78, R79, R80, R81, R98, R147 | Resistor, Resistor, Resistor, Resistor, Resistor, Resistor, Resistor, Resistor, 56, 56 | RESC1608X06L | Top
2 | 100 | R135, R150 | Resistor | RESC1608X06L | Top
2 | 180 | R107, R137 | Resistor | RESC1608X06L | Top
2 | 1nF | C53, C54 | Capacitor | CAPC1608X08L | Top
2 | 1uF | C56, C61 | Capacitor | CAPC1608X08L | Top
2 | 200 | R99, R148 | 200 | RESC1608X06L | Top
2 | 5.6K | R115, R116 | Resistor | RESC1608X06L | Top
2 | 82 | R100, R149 | 82 | RESC1608X06L | Top
2 | BAT54S | D33, D34 | Schottky Barrier Double Diode | SOT23_N | Top
2 | QBLP679E-RGB | D27, D38 |  | QBLP679E-RGB | Top
2 | SN74HC595PWR | U14, U16 | 8-Bit Serial-Input/Serial or Prallel-Output Shift Register with Latched 3-State Outputs | 948F-01_N | Top
21 | 100nF | C1, C3, C6, C10, C11, C12, C13, C23, C24, C27, C29, C33, C35, C36, C37, C38, C39, C62, C65, C66, C67 | Capacitor | CAPC1608X08L | Top
22 | BC817-40 | Q5, Q6, Q8, Q9, Q10, Q11, Q13, Q14, Q15, Q16, Q17, Q18, Q31, Q32, Q34, Q37, Q38, Q39, Q40, Q42, Q45, Q46 | NPN General-purpose Transistor | SOT23_N | Top
3 | 1.5K | R26, R46, R47 | 120 | RESC1608X06L | Top
3 | 27-21/BHC-AN1P2/3C | D8, D31, D37 | SMD Blue led right angle mount 3.3V@20ma 28mcd | 27-21 Everlight Blue | Top
3 | 27-21SURC/S530-A3 | D7, D32, D36 | SMD Red led right angle mount 2V@20ma 57mcd | 27-21 EVERLIGHT | Top
3 | 47nF | C58, C59, C60 | Capacitor | CAPC1608X08L | Top
3 | APTD1608CGCK | D28, D29, D30 | LED standard - CMS Helios SMD Green 570nm 230mcd | DIOC1608X08N | Top
4 | 19-21SURC/S530-A3/TR8 | D1, D3, D4, D5 | SMD Red 0603 2V@20ma 56 mcd | DIOC1608X08N | Top
4 | AP7331-33WG-7 | U18, U22, U24, U27 | 300mA, Low Quiescent Current, Fast Transient LDO | SOT95P285X100-5N | Top
5 | 100K | R138, R139, R141, R143, R159 | Resistor | RESC1608X06L | Top
5 | 10uF | C2, C4, C31, C46, C76 | Capacitor | CAPC1608X08L | Top
6 | 1K | R25, R48, R49, R108, R166, R167 | 120, 120, 120, Resistor, 120, 120 | RESC1608X06L | Top
6 | 22K | R11, R42, R43, R67, R130, R142 | 120, 120, 120, Resistor, Resistor, Resistor | RESC1608X06L | Top
6 | 39 | R66, R86, R87, R88, R89, R134 | Resistor | RESC1608X06L | Top
6 | 4.7K | R92, R93, R94, R144, R145, R146 | Resistor | RESC1608X06L | Top
6 | 6.2 | R36, R37, R39, R40, R54, R55 | 120 | RESC1608X06L | Top
7 | ITR9909 | U6, U7, U8, U9, U10, U11, U12 | Everlight Opto Interrupter | ITR9909_EDGE | Top
8 | 10K | R101, R102, R109, R110, R117, R118, R128, R129 | Resistor | RESC1608X06L | Top
8 | 4.7uF | C32, C44, C45, C47, C48, C49, C50, C77 | Capacitor | CAPC1608X08L | Top
8 | APTD1608SYCK | D13, D14, D15, D16, D21, D22, D23, D24 | LED standard - CMS Helios SMD Yellow 590nm 480mcd | DIOC1608X08N | Top
9 | 2.2K | R32, R34, R35, R41, R52, R53, R103, R104, R126 | Resistor | RESC1608X06L | Top

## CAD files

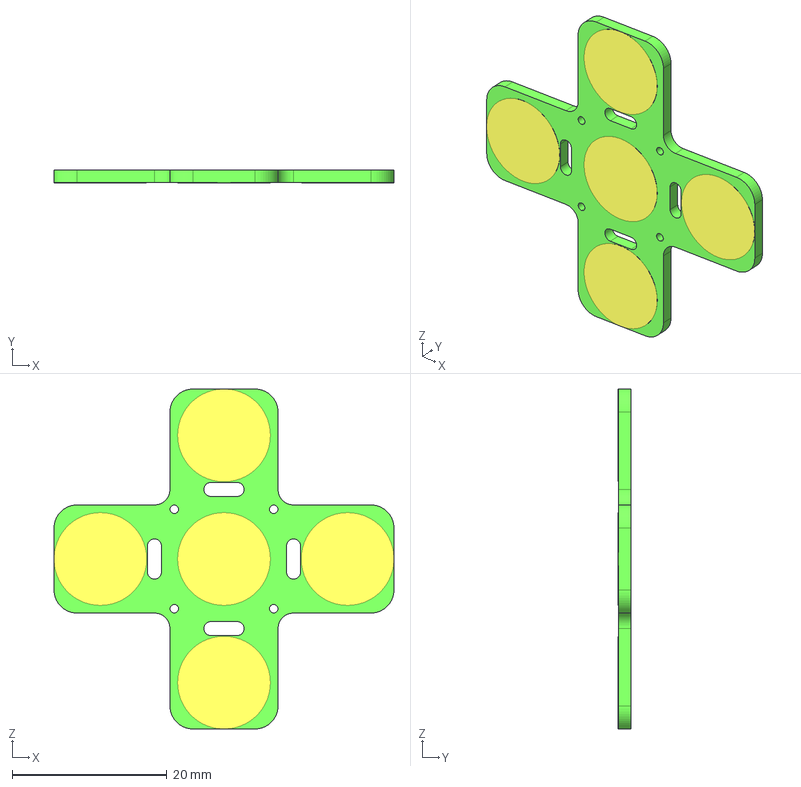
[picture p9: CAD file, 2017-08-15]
Models/pcb-capacitif.stp
44.0 x 1.63 x 44.0 mm

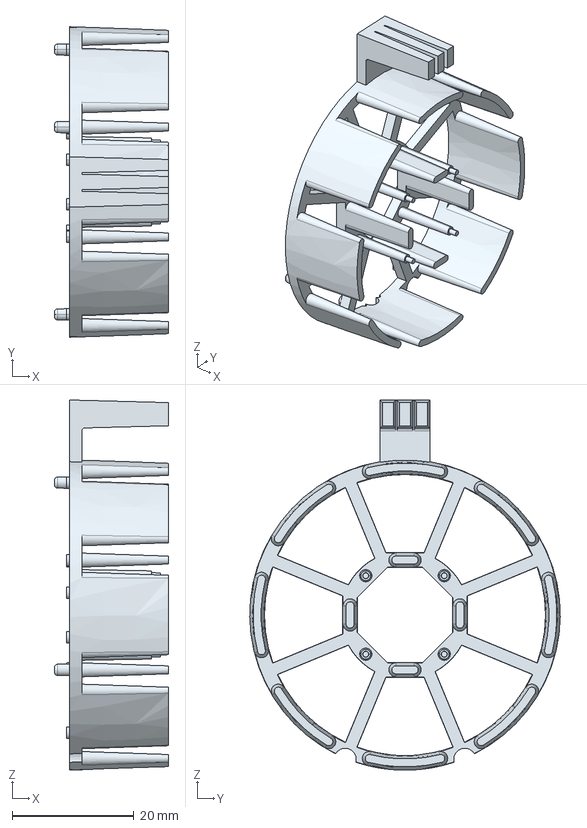
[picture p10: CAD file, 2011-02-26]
Models/p_guide-onde.stp
18.7 x 50.9 x 60.7 mm

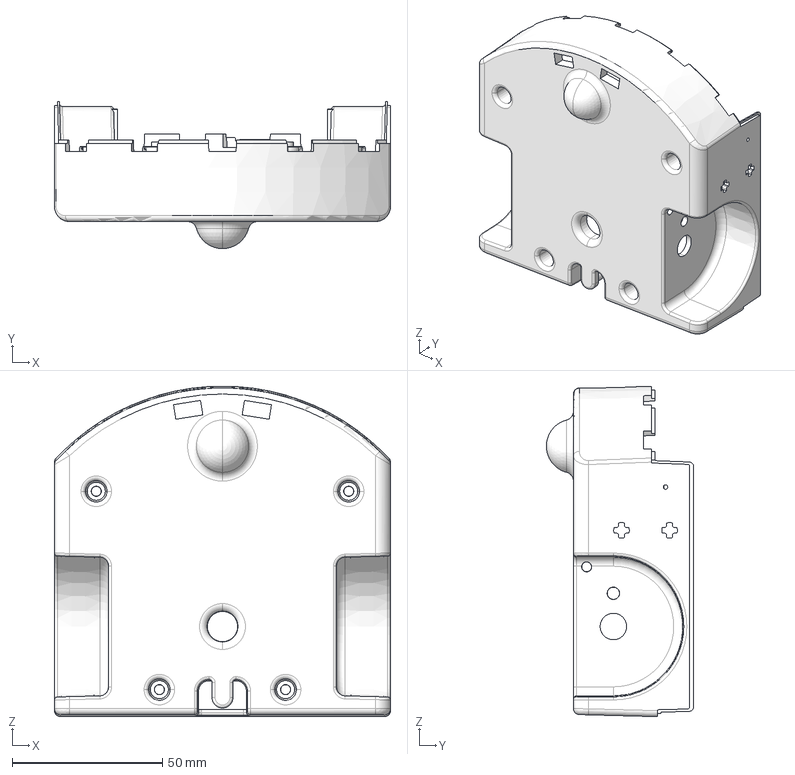
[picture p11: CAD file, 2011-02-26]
Models/p_coque_dessous_prt.stp
111.8 x 49.0 x 109.9 mm

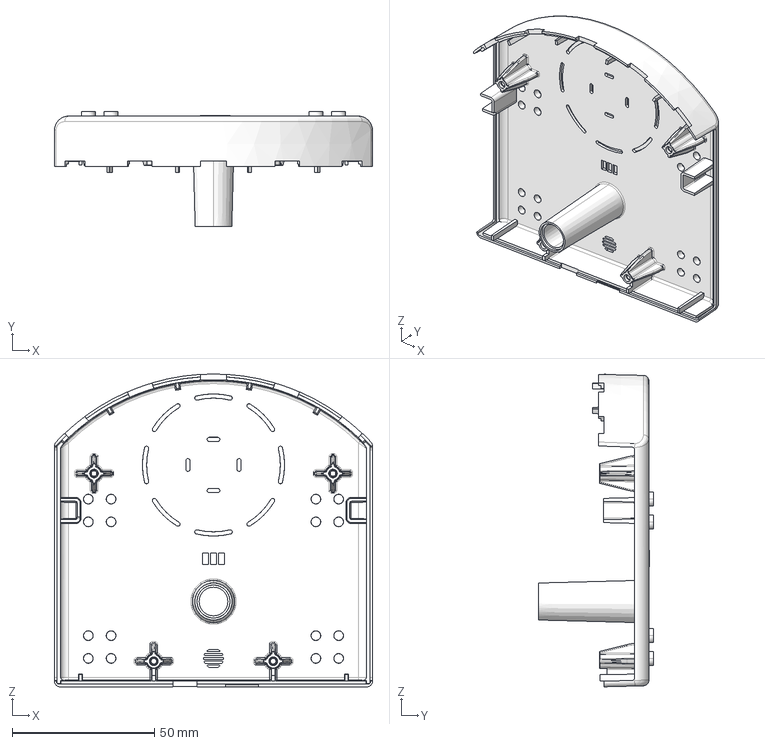
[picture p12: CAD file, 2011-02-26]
Models/p_coque_dessus_prt.stp
111.8 x 40.4 x 109.9 mm

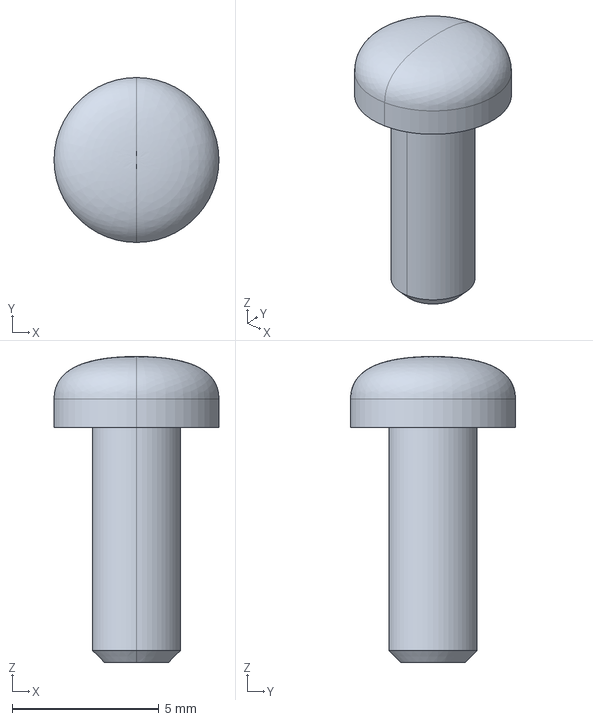
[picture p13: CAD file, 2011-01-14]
Models/delta_pt-30-8_prt.stp
5.61 x 5.61 x 10.4 mm

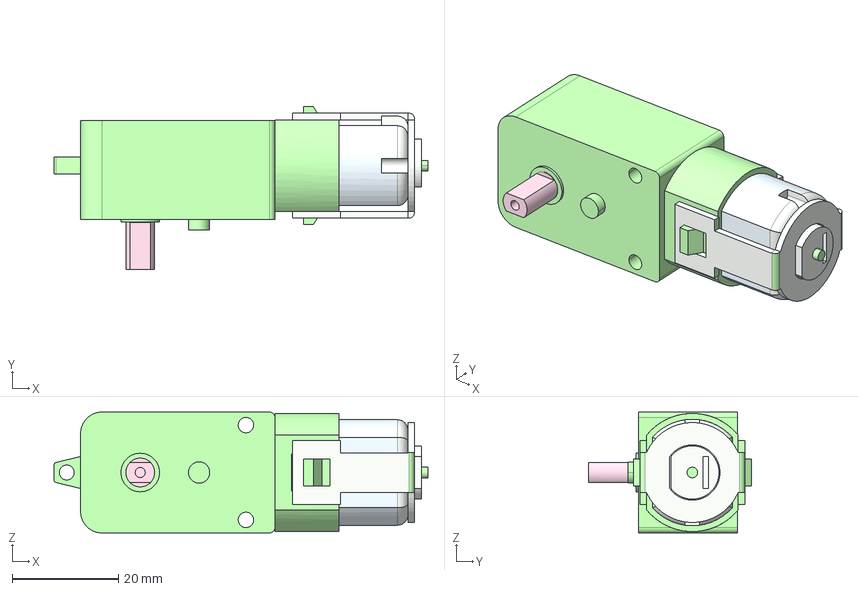
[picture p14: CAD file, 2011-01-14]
Models/motor_gp01s-a130_prt.stp
70.2 x 30.6 x 22.7 mm

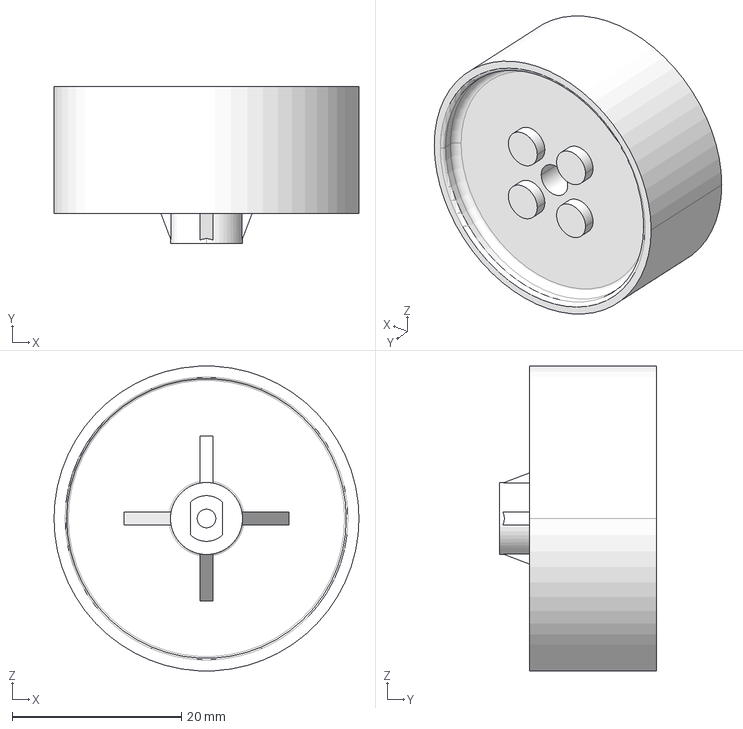
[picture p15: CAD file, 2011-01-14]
Models/p_roue_interieur_prt.stp
36.0 x 18.5 x 35.9 mm

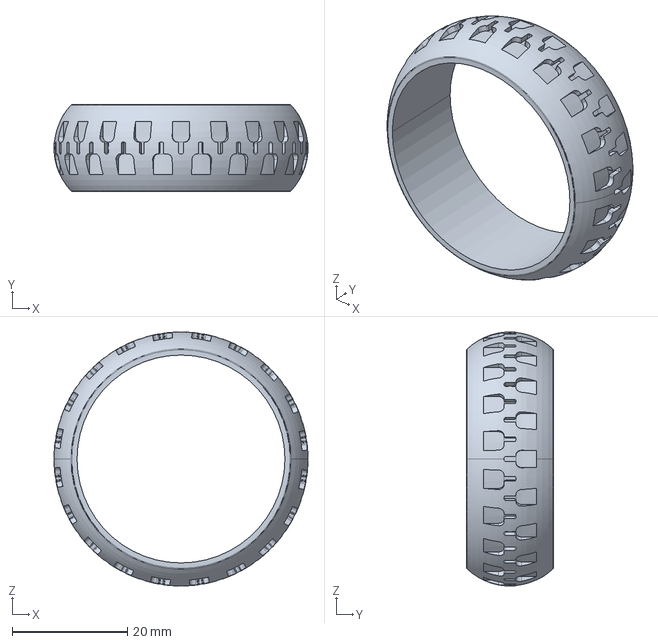
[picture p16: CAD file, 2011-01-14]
Models/p_roue_surmoulage_prt.stp
44.0 x 15.0 x 44.0 mm

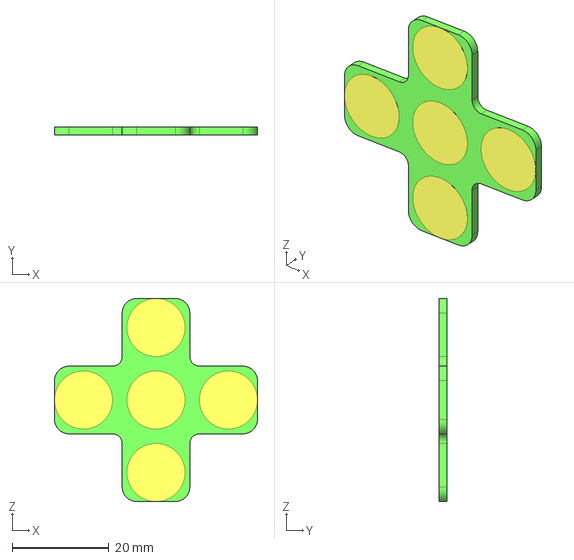
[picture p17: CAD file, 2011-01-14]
Models/pcb-capacitif_prt.stp
42.0 x 1.63 x 42.0 mm

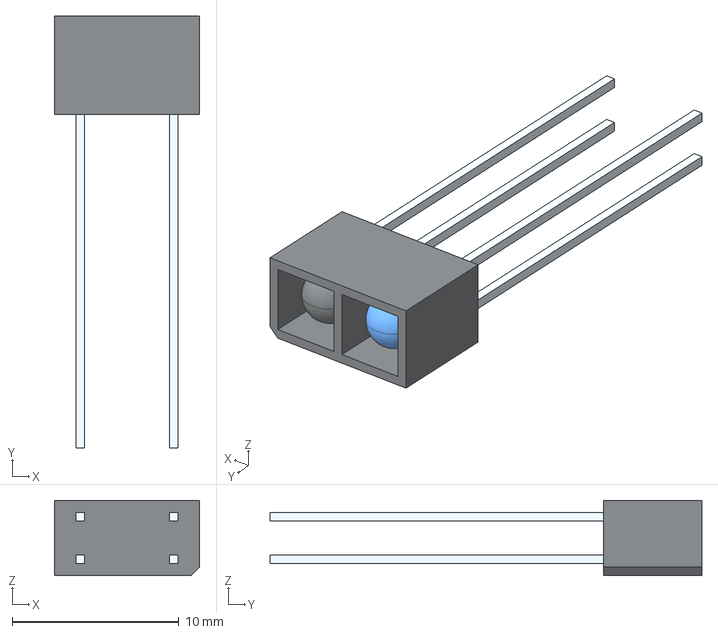
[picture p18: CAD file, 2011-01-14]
Models/itr9909long_prt.stp
8.70 x 25.9 x 4.50 mm

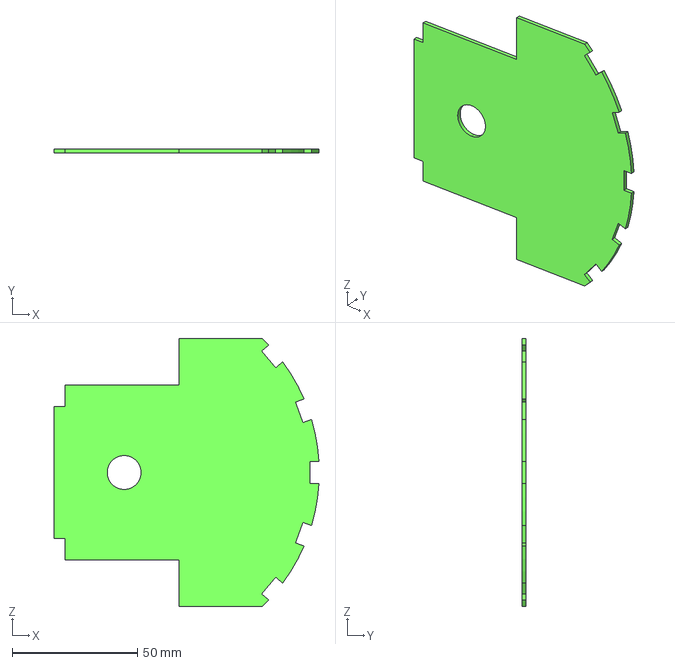
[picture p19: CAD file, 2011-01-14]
Models/pcb_prt.stp
105.7 x 1.60 x 107.0 mm

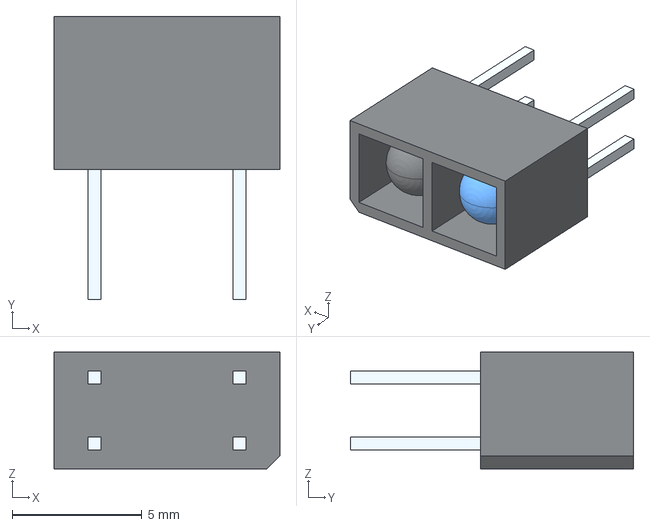
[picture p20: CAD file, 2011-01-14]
Models/itr9909_prt.stp
8.70 x 10.9 x 4.50 mm

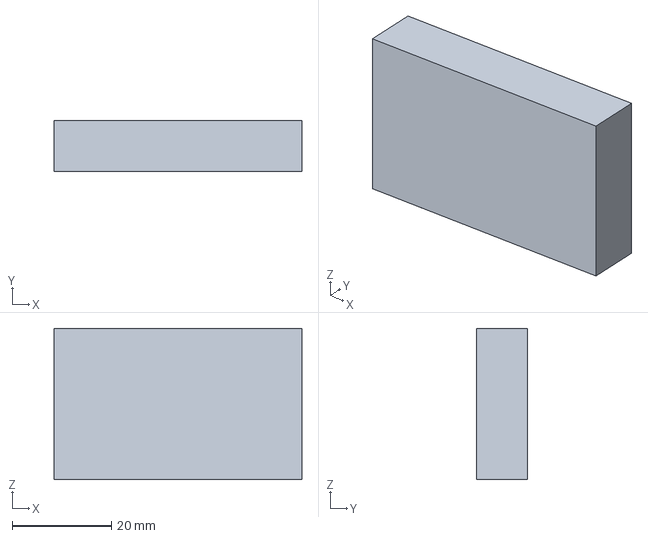
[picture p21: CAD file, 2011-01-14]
Models/batt_103048_prt.stp
50.0 x 10.2 x 30.5 mm

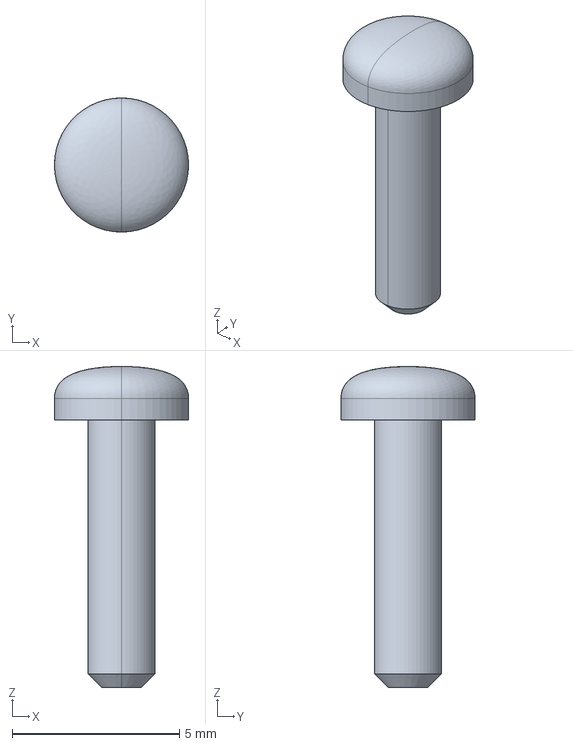
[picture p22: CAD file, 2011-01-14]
Models/delta_pt-20-8_prt.stp
4.01 x 4.01 x 9.60 mm

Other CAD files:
Models/a_thymio_2_asm.stp

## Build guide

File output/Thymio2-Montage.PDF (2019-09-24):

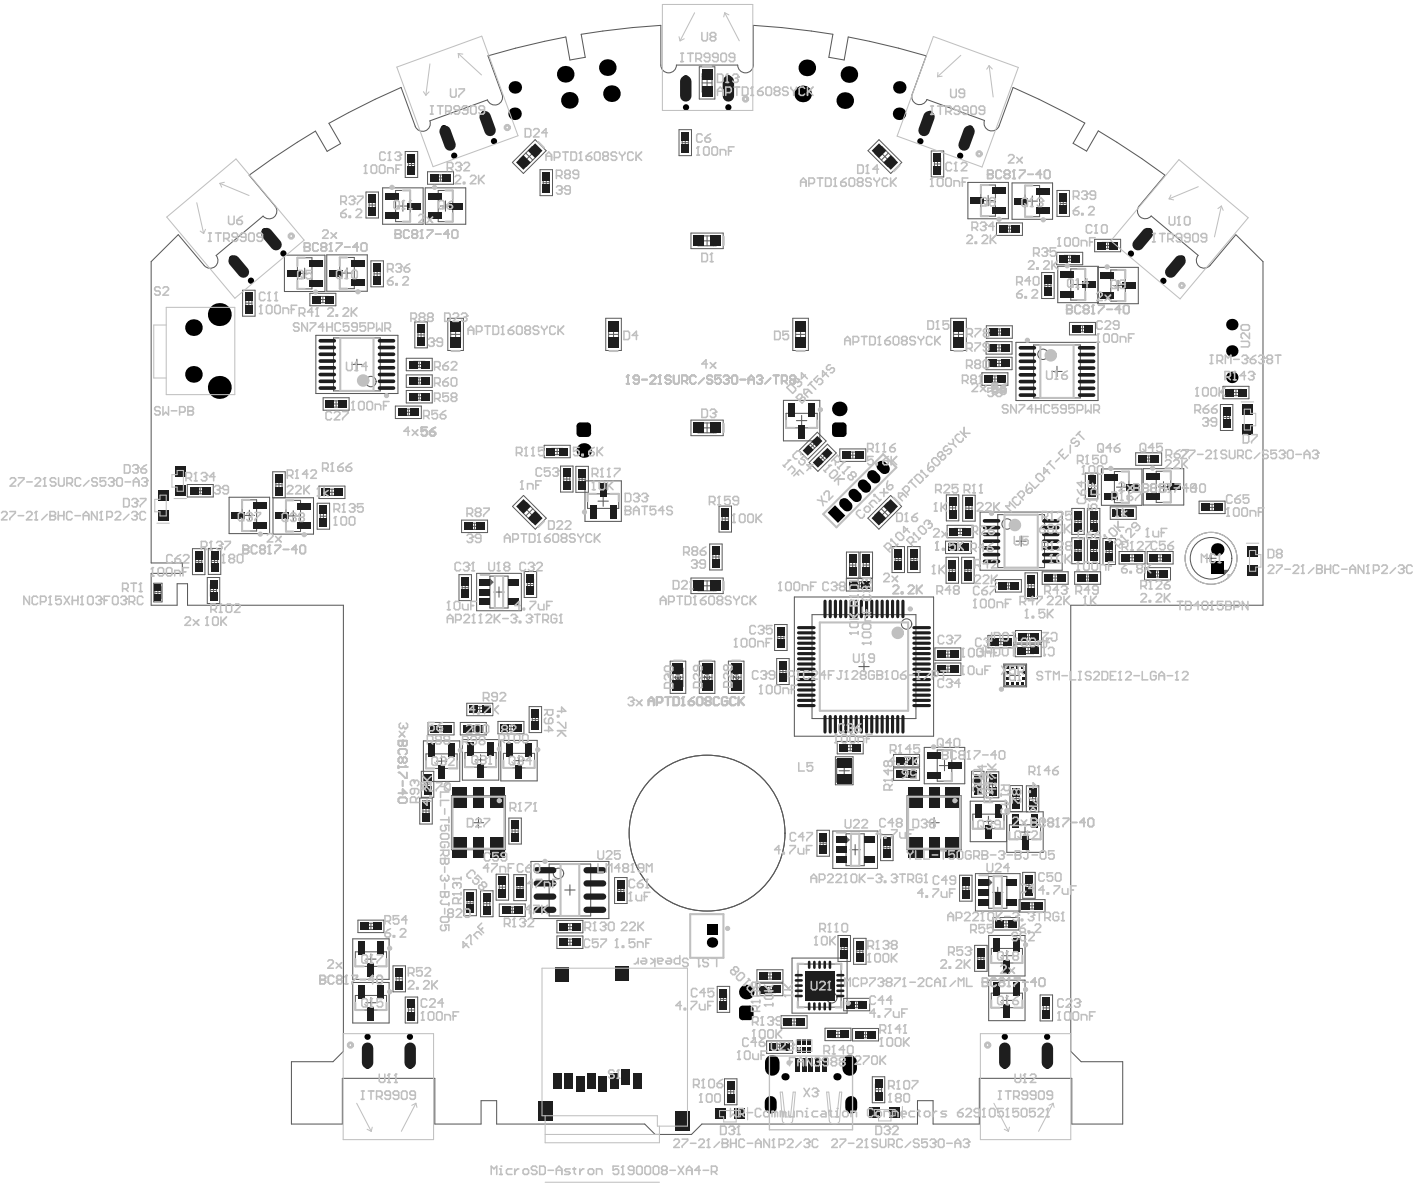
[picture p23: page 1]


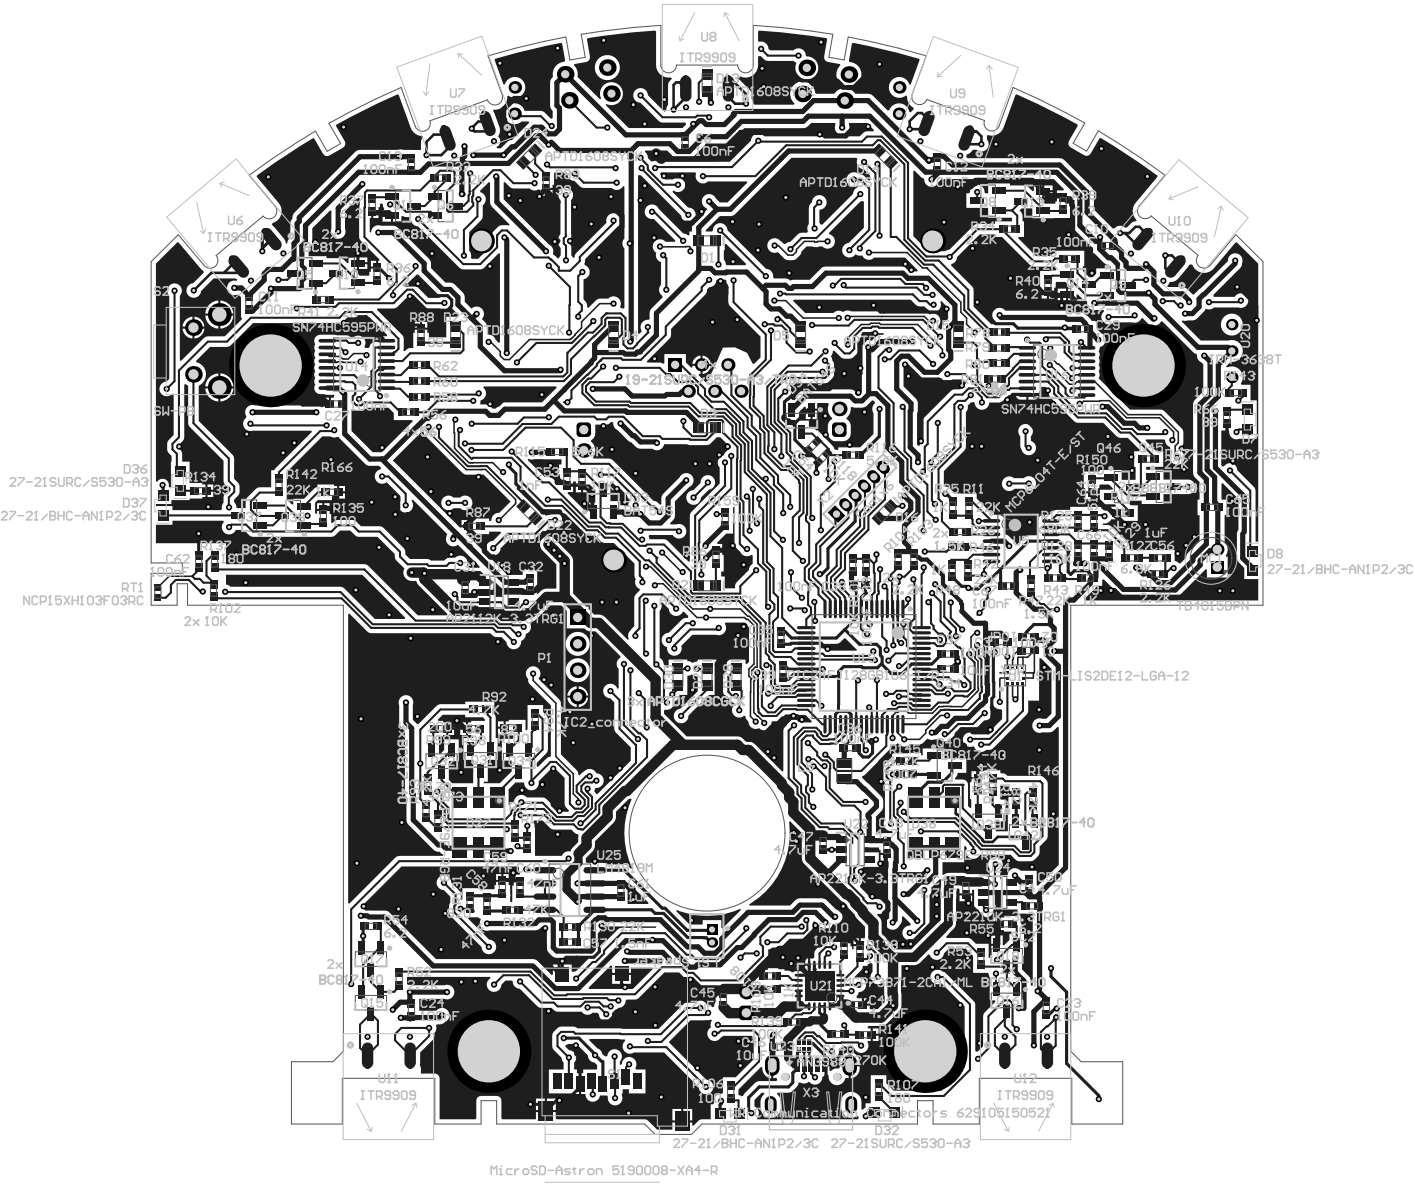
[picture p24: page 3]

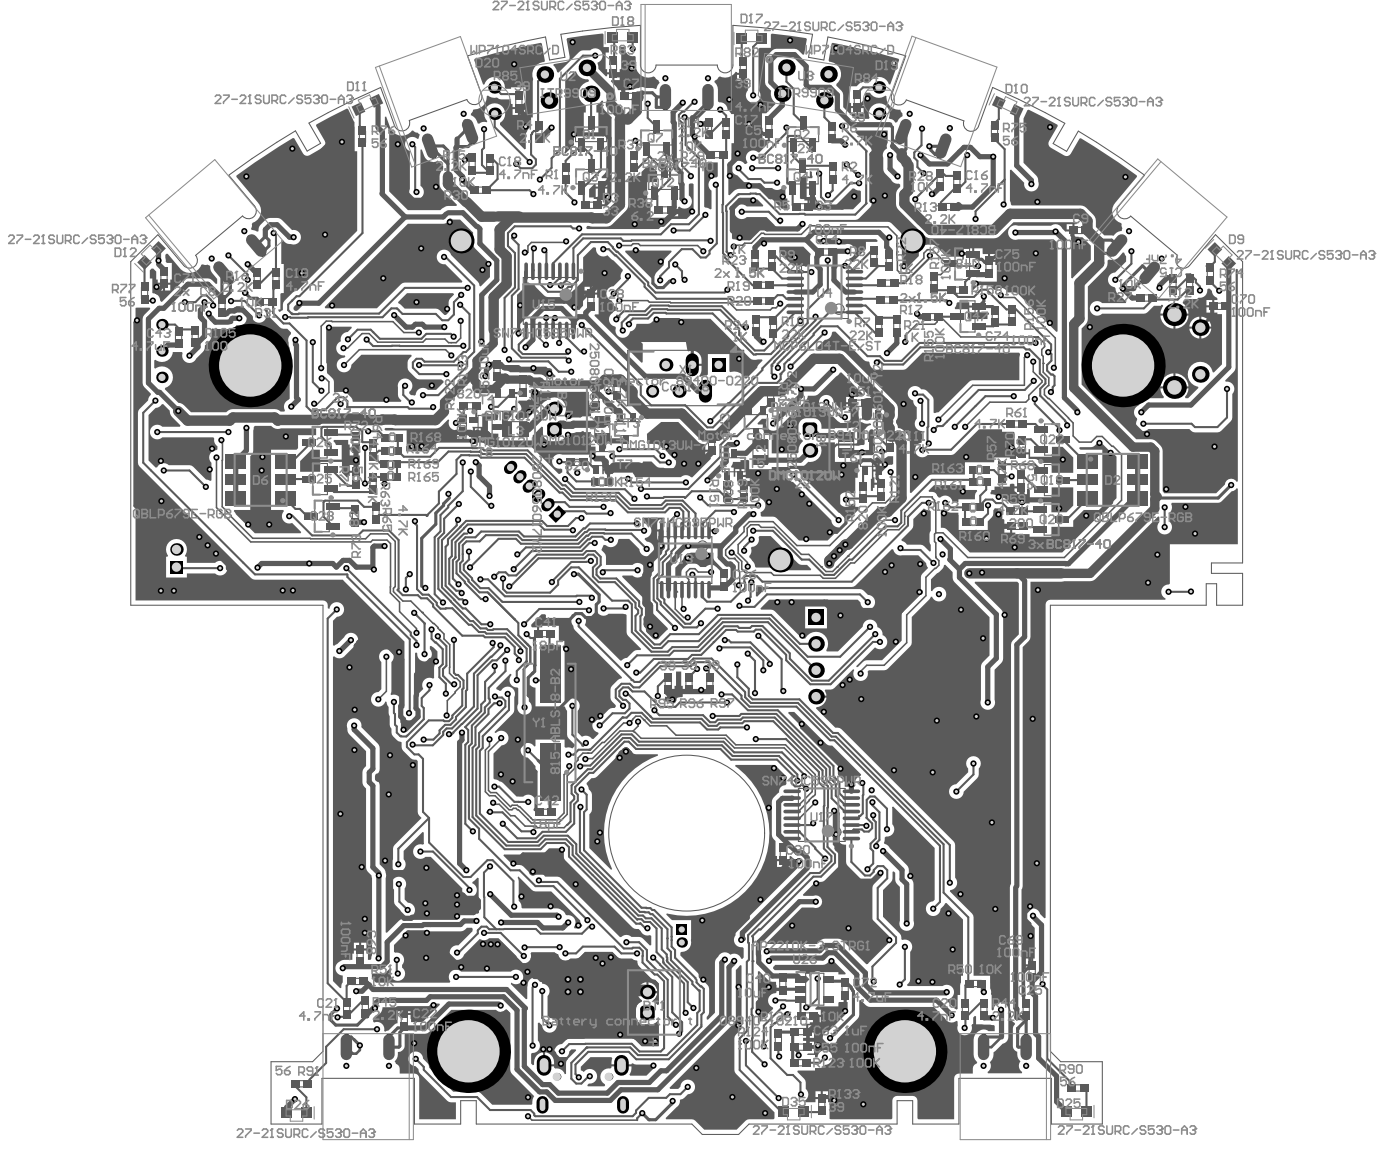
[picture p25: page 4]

Quantity | Comment | Designator | Description | Footprint
2 Motor connector 89400-022B1, B2 | | | Motor, General Kind | BAT-2
1 | Battery connector t 08940BT1 | | Multicell Battery | BAT-2
38 100nF | | C1, C3, C5, C6, C7, C8, C9, C10, C11, Cap acitor | | CAP C100 5X05N
8 10uF | | C2, C31, C40, C46, C51, C52, C73, C78Capacitor | | CAPC1005X05N
2 51pF | | C4, C64 | Capacitor | CAPC1005X05N
7 | 4.7nF | C15, C16, C17, C18, C19, C20, C21 | Capacitor | CAPC1005X05N
9 4.7uF | | C32, C43, C44, C45, C47, C48, C49, C5Ca pacitor | | CAPC1005X05N
1 | 10uF X5R | C34 | Capacitor | CAPC1005X05N
2 18pF | | C41, C42 | | CAPC1005X05N
2 1nF | | C53, C54 | Capacitor | CAPC1005X05N
3 1uF | | C56, C61, C63 | Capacitor | CAPC1005X05N
1 | 1.5nF | C57 | Capacitor | CAPC1005X05N
3 47nF | | C58, C59, C60 | Capacitor | CAPC1005X05N
4 19-21SURC/S530-A3/TR8 | | D1, D3, D4, D5 | SMD Red 0603 2V@20ma 56 mcd | DIOC1608X08N
4 YLL-T50GRB-3-BJ-05 | | D2, D6, D27, D38 | | QBLP679E-RGB
12 27-21SURC/S530-A3 | | D7, D9, D10, D11, D12, D17, D18, D2S MDR edled righ tangle mount 2V@227-21EVERLIGHT
3 27-21/BHC-AN1P2/3C | | D8, D31, D37 | SMD Blue led right angle mount 3.3 27- 1Everlight Blue
8 APTD1608SYCK | | D13, D14, D15, D16, D21, D22, D23, | DLED standard - CMS Helios SMD YeDIOC1608X08N
2 WP7104SRC/D | | D19, D20 | Red led 2V@20ma 57mcd | LED_TH_3MM_20MM
3 APTD1608CGCK | | D28, D29, D30 | LED standard - CMS Helios SMD GrDIOC1608X08N
2 BAT54S | | D33, D34 | Schottky Barrier Double Diode | SOT23_N
5 2508056017Y2 | | L1, L2, L3, L4, L5 | SMD EMI Suppression Ferrite BeadINDC2012 X11L
1 | Speaker | LS1 | Loudspeaker | PIN2
1 | TD4015BPN | MC1 | Omnidirectional Back Electret CondMICRO_TD4015BPN
36 BC817-40 | | Q1, Q2, Q3, Q4, Q5, Q6, Q7, Q8, Q9, | NPN Gen eral-p urpo seTr ansisto r | S OT2 3_N
18 4.7K | | R1, R2, R57, R59, R61, R63, R64, R65, Resis tor | | RES C1005 X04N
2 33 | | R3, R5 | 120, Resistor | RESC1005X04N
2 2.7K | | R4, R6 | Resistor | RESC1005X04N
10 22K | | R7, R8, R9, R10, R11, R42, R43, R67, | R120, Resistor | RESC1005X04N
17 | 2.2K | R12, R13, R14, R15, R16, R32, R33, R312 0, Re sisto r | | RES C100 5X04N
7 | 1.5K | R17, R18, R19, R20, R26, R46, R47 | 120 | RESC1005X04N
10 1K | | R21, R22, R23, R24, R25, R48, R49, R1120 , Resis tor | | RESC1005X04N
16 10K | | R27, R28, R29, R30, R31, R50, R51, R1120 , Resis tor | | RESC 1005X 04N
7 | 6.2 | R36, R37, R38, R39, R40, R54, R55 | 120 | RESC1005X04N
18 56 | | R56, R58, R60, R62, R69, R72, R74, R7Re sisto r, 56 | | RE SC1 005X0 4N
14 39 | | R66, R82, R83, R84, R85, R86, R87, R8Re sisto r | | RESC1005X04N
4 200 | | R68, R71, R98, R147 | 200 | RESC1005X04N
4 82 | | R70, R73, R100, R149 | 82 | RESC1005X04N
4 100 | | R105, R106, R135, R150 | Resistance, Resistor | RESC1005X04N
2 180 | | R107, R137 | Resistor | RESC1005X04N
2 5.6K | | R115, R116 | Resistor | RESC1005X04N
15 100K | | R119, R120, R121, R122, R123, R124, | Resis tor | R ESC1 005X0 4N
1 | 680K | R125 | Resistor | RESC1005X04N
1 | 6.8K | R127 | Resistor | RESC1005X04N
5 820 | | R131, R151, R152, R153, R154 | Resistor | RESC1005X04N
1 | 47K | R132 | Resistor | RESC1005X04N
1 | 270K | R140 | Resistor | RESC1005X04N
6 0 | | R160, R161, R168, R169, R170, R171 | Resistor | RESC1005X04N
1 | NCP15XH103F03RC | RT1 | Thermistors - NTC 10K OHM 1% 04RESC1005X04L
1 | MicroSD-Astron 5190008-XA4S1 | | MicroSD Card connector 5190008-XAstron 5190008-XA4-R
1 | SW-PB | S2 | Switch | FSMRA2JH
4 DMG1013UW-7 | | T1, T2, T3, T4 | Transistor MOSFET 1 x P Pining : 1=SO T65P 210X100-3N
4 DMG1012UW | | T5, T6, T7, T8 | Transistor MOSFET 1 x N, Pining : 1SOT 65P2 10X100-3N
1 | STM-LIS2DE12-LGA-12 | U1 | | STM-LGA-12
2 ITR9909 | | U2, U3 | Everlight Opto Interrupter | ITR9909_LONG
2 MCP6L04T-E/ST | | U4, U5 | 1MHz, 85 µA Quad Op Amp, 14-PinTSSOP-S T14_N
7 | ITR9909 | U6, U7, U8, U9, U10, U11, U12 | Everlight Opto Interrupter | ITR9909_EDGE
5 SN74HC595PWR | | U13, U14, U15, U16, U17 | 8-Bit Serial-Input/Serial or Prallel-O948F-01_N
1 | AP2112K-3.3TRG1 | U18 | 300mA, Low Quiescent Current, FaSOT95P285X100-5N
1 | PIC24FJ128GB106-I/PT | U19 | General Purpose 16-Bit Flash MicroTQFP-PT64_N
1 | IRM-3638T | U20 | IR Receiver Module (38 kHz) for ReIR-receiver
1 | MCP73871-2CAI/ML | U21 | Stand-Alone System Load Sharing QFN-ML20_N
3 AP2210K-3.3TRG1 | | U22, U24, U26 | 300mA, Low Quiescent Current, FaSOT95P285X100-5N
1 | FAN3988 | U23 | USB/Charger and Over Voltage DeMLP1.45X1MM
1 | LM4819M | U25 | 350mW Audio Power Amplifier withM08A_N
1 | Con1x6 | X2 | 1 x 6 pins connector | MHDR1X6
1 | WR-Communication ConneX3 | | WR-COM_USB_Micro Type B_Hor629105150521
1 | 815-ABLS-8-B2 | Y1 | Surface Mount Quartz Crystal 8MhzHC49/4H_SMX

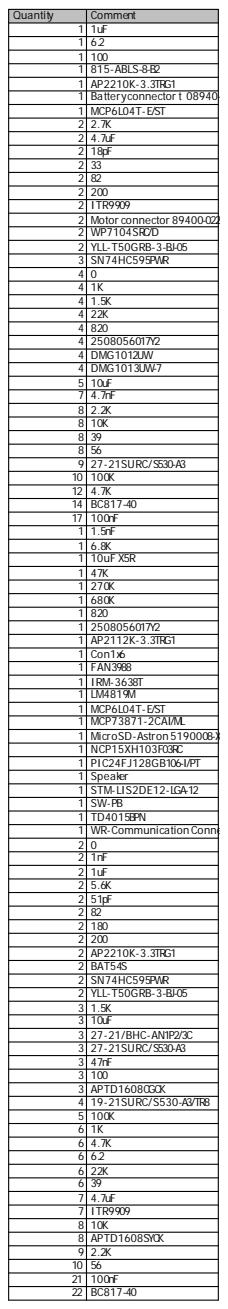
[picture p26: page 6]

Quantity | Comment

1 | 1uF
1 | 6.2
1 | 100
1 | 815-ABLS-8-B2
1 | AP2210K-3.3TRG1
1 | Batteryconnector t 08940-
1 | MCP6L04T-E/ST
2 | 2.7K
2 | 4.7uF
2 | 18pF
2 | 33
2 | 82
2 | 200
2 | ITR9909
2 | Motor connector 89400-022
2 | WP7104SRC/D
2 | YLL-T50GRB-3-BJ-05
3 | SN74HC595PWR
4 | 1K
4 | 1.5K
4 | 22K
4 | 820
4 | 2508056017Y2
4 | DMG1012UW
4 | DMG1013UW-7
5 | 10uF
7 | 4.7nF
8 | 2.2K
8 | 10K
8 | 39
8 | 56
9 | 27-21SURC/S530-A3
10 | 100K
12 | 4.7K
14 | BC817-40
17 | 100nF
1 | 1.5nF
1 | 6.8K
1 | 10uF X5R
1 | 47K
1 | 270K
1 | 680K
1 | 820
1 | 2508056017Y2
1 | AP2112K-3.3TRG1
1 | Con1x6
1 | FAN3988
1 | IRM-3638T
1 | LM4819M
1 | MCP73871-2CAI/ML
1 | MicroSD-Astron 5190008-X
1 | NCP15XH103F03RC
1 | PIC24FJ128GB106-I/PT
1 | Speaker
1 | STM-LIS2DE12-LGA-12
1 | SW-PB
1 | TD4015BPN
1 | WR-Communication Conne
2 | 1nF
2 | 1uF
2 | 5.6K
2 | 51pF
2 | 180
2 | AP2210K-3.3TRG1
2 | BAT54S
2 | SN74HC595PWR
3 | 1.5K
3 | 10uF
3 | 27-21/BHC-AN1P2/3C
3 | 27-21SURC/S530-A3
3 | 47nF
3 | 100
3 | APTD1608CGCK
4 | 19-21SURC/S530-A3/TR8
5 | 100K
6 | 1K
6 | 4.7K
6 | 6.2
6 | 22K
6 | 39
7 | 4.7uF
7 | ITR9909
8 | APTD1608SYCK
9 | 2.2K
10 | 56
21 | 100nF
22 | BC817-40

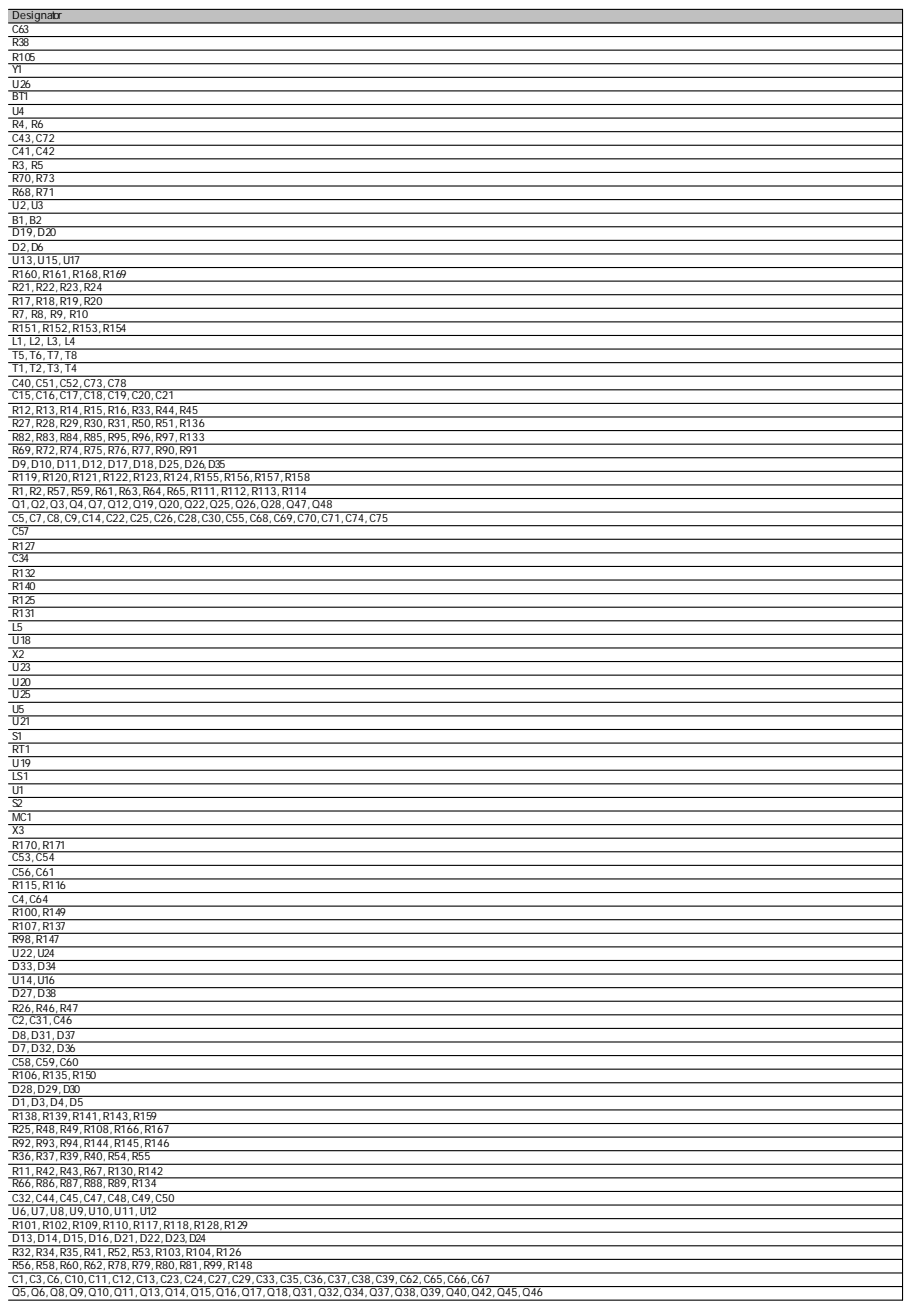
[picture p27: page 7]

Description | Footprint | Layer
Capacitor | CAPC1005X05N | Bottom
120 | RESC1005X04N | Bottom
Resistance | RESC1005X04N | Bottom
Surface MountQuartzCrystal 8Mhz HC49/4H_SMX | Bottom
300mA, LowQuiescentCurrent,FaSOT95P285X100-5N | Bottom
Multicell Battery | BAT-2 | Bottom
1 MHz,85 µAQuad Op Amp,14-PinTSSOP-ST14_N | Bottom
Resistor | RESC1005X04N | Bottom
Capacitor | CAPC1005X05N | Bottom
| CAPC1005X05N | Bottom
120,Resistor | RESC1005X04N | Bottom
82 | RESC1005X04N | Bottom
200 | RESC1005X04N | Bottom
EverlightOpto Interrupter | ITR9909_LONG | Bottom
Motor,General Kind | BAT-2 | Bottom
Red led 2V@20ma 57mcd | LED_TH_3MM_20MM | Bottom
| QBLP679E-RGB | Bottom
8-BitSerial-Input/Serial or Pralle948F-01_N | Bottom
Resistor | RESC1005X04N | Bottom
120 | RESC1005X04N | Bottom
120 | RESC1005X04N | Bottom
120 | RESC1005X04N | Bottom
Resistor | RESC1005X04N | Bottom
SMD EMI Suppression Ferrite BeaINDC2012X11L | Bottom
Transistor MOSFET1 xN,Pining :1SOT65P210X100-3N | Bottom
Transistor MOSFET1 xP Pining :1=SOT65P210X100-3N | Bottom
Capacitor | CAPC1005X05N | Bottom
Capacitor | CAPC1005X05N | Bottom
120,Resistor | RESC1005X04N | Bottom
120,Resistor | RESC1005X04N | Bottom
Resistor | RESC1005X04N | Bottom
56,Resistor | RESC1005X04N | Bottom
SMD Red led rightangle mount2V27-21EVERLIGHT | Bottom
Resistor | RESC1005X04N | Bottom
Resistor | RESC1005X04N | Bottom
NPN General-purpose Transistor | SOT23_N | Bottom
Capacitor | CAPC1005X05N | Bottom
Capacitor | CAPC1005X05N | Top
Resistor | RESC1005X04N | Top
Capacitor | CAPC1005X05N | Top
Resistor | RESC1005X04N | Top
Resistor | RESC1005X04N | Top
Resistor | RESC1005X04N | Top
Resistor | RESC1005X04N | Top
SMD EMI Suppression Ferrite BeaINDC2012X11L | Top
300mA, LowQuiescentCurrent,FaSOT95P285X100-5N | Top
1 x6 pins connector | MHDR1X6 | Top
USB/Charger and Over Voltage DeMLP1.45X1MM | Top
IRReceiver Module (38 kHz)for ReIR-receiver | Top
350mWAudio Power Amplifier witM08A_N | Top
1 MHz,85 µAQuad Op Amp,14-PinTSSOP-ST14_N | Top
Stand-Alone System Load SharingQF N-ML20_N | Top
MicroSD Card connector 5190008-Astron 5190008-XA4-R | Top
Thermistors - NTC10KOHM1% 04RESC1005X04L | Top
General Purpose 16-BitFlash MicrTQFP-PT64_N | Top
Loudspeaker | PIN2 | Top
| STM-LGA-12 | Top
Switch | FSMRA2JH | Top
Omnidirectional BackElectretConMICRO_ TD4015BPN | Top
WR-COM_USB_Micro Type B_Hori629105150521 | Top
Resistor | RESC1005X04N | Top
Capacitor | CAPC1005X05N | Top
Capacitor | CAPC1005X05N | Top
Resistor | RESC1005X04N | Top
Capacitor | CAPC1005X05N | Top
82 | RESC1005X04N | Top
Resistor | RESC1005X04N | Top
200 | RESC1005X04N | Top
300mA, LowQuiescentCurrent,FaSOT95P285X100-5N | Top
SchottkyBarrier Double Diode | SOT23_N | Top
8-BitSerial-Input/Serial or Pralle948F-01_N | Top
| QBLP679E-RGB | Top
120 | RESC1005X04N | Top
Capacitor | CAPC1005X05N | Top
SMD Blue led rightangle mount3.27-21EverlightBlue | Top
SMD Red led rightangle mount2V27-21EVERLIGHT | Top
Capacitor | CAPC1005X05N | Top
Resistance,Resistor | RESC1005X04N | Top
LED standard - CMSHeliosSMD GrDIOC1608X08N | Top
SMD Red 0603 2V@20ma 56 mcd | DIOC1608X08N | Top
Resistor | RESC1005X04N | Top
120,Resistor | RESC1005X04N | Top
Resistor | RESC1005X04N | Top
120 | RESC1005X04N | Top
120,Resistor | RESC1005X04N | Top
Resistor | RESC1005X04N | Top
Capacitor | CAPC1005X05N | Top
EverlightOpto Interrupter | ITR9909_EDGE | Top
Resistor | RESC1005X04N | Top
LED standard - CMSHeliosSMD YeDIOC1608X08N | Top
Resistor | RESC1005X04N | Top
Resistor,56 | RESC1005X04N | Top
Capacitor | CAPC1005X05N | Top
NPN General-purpose Transistor | SOT23_N | Top

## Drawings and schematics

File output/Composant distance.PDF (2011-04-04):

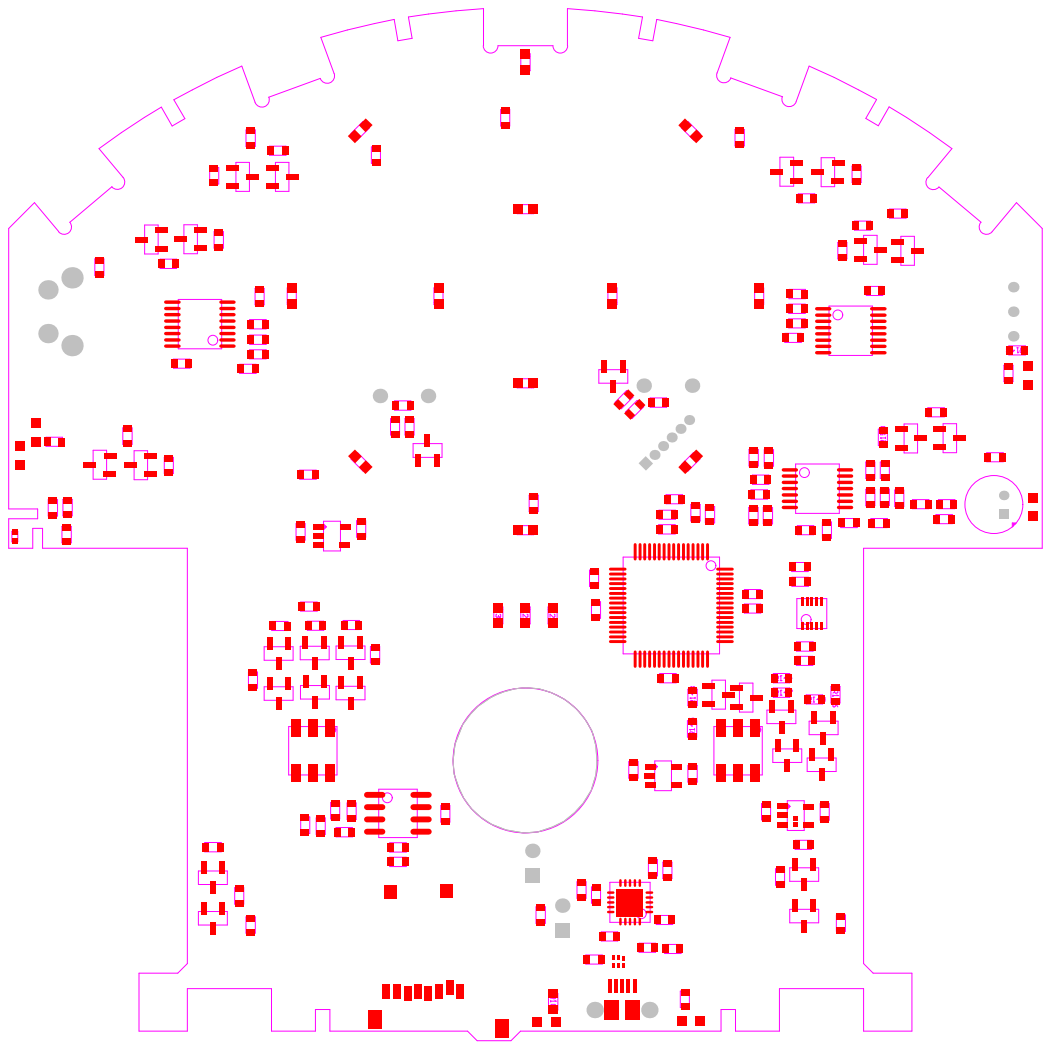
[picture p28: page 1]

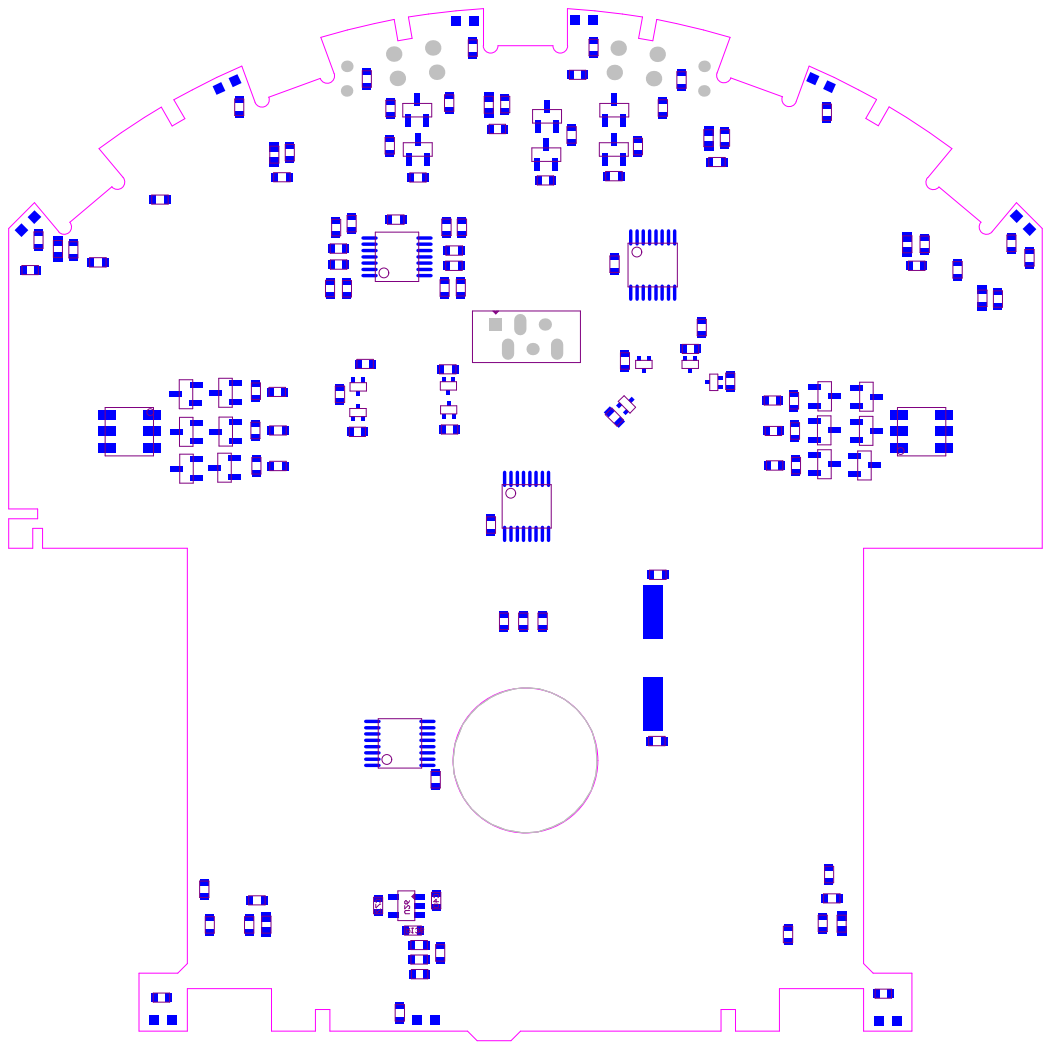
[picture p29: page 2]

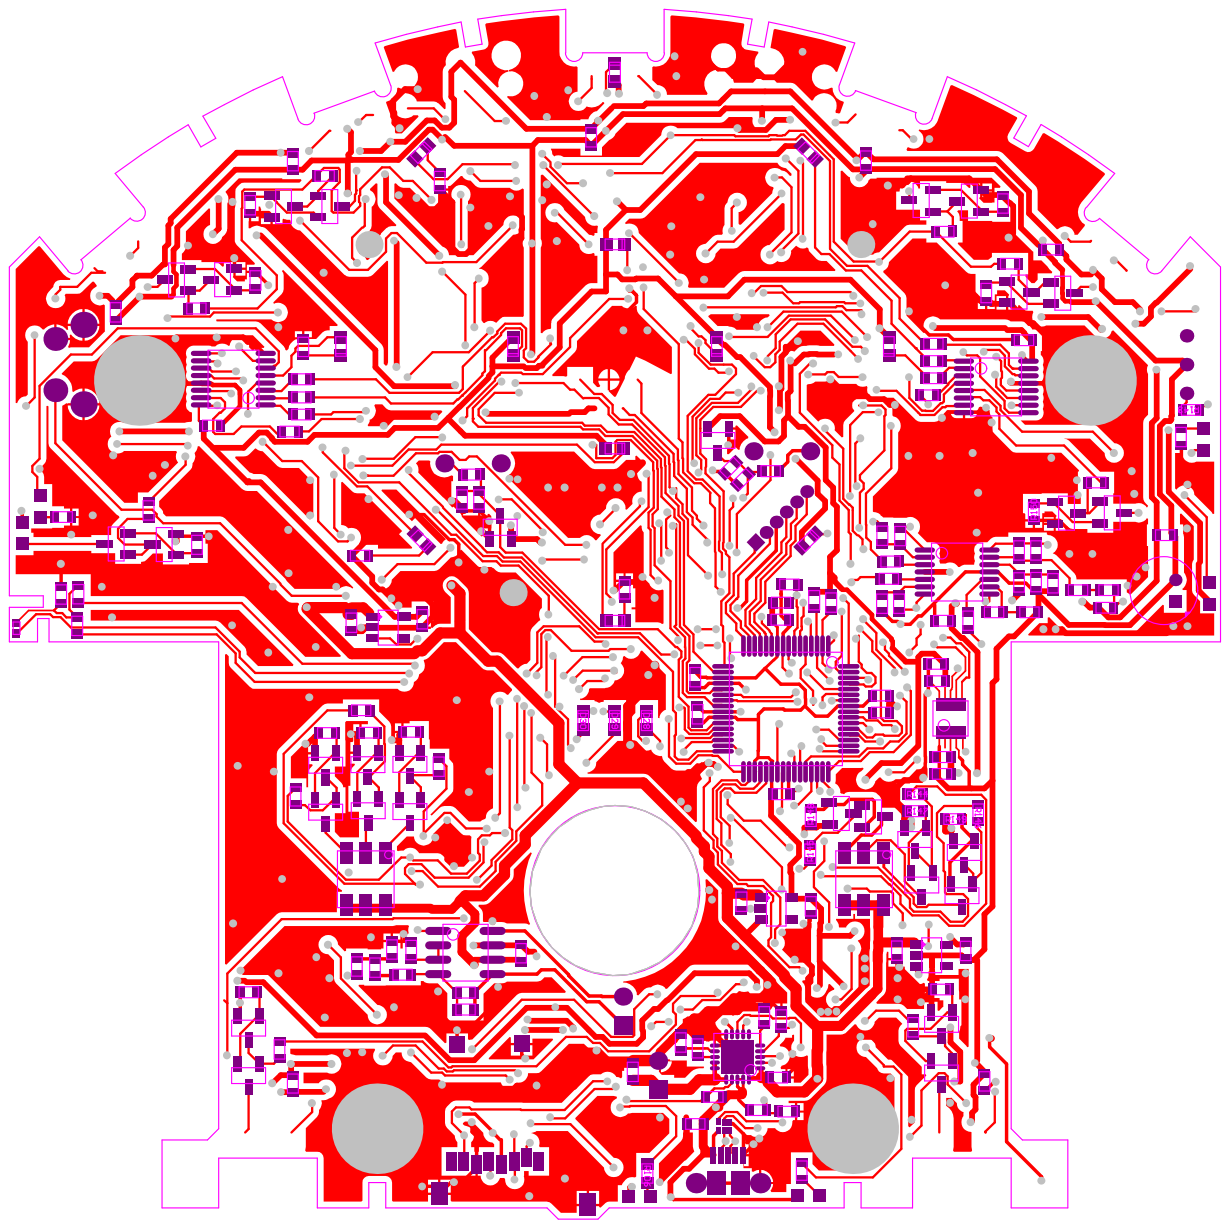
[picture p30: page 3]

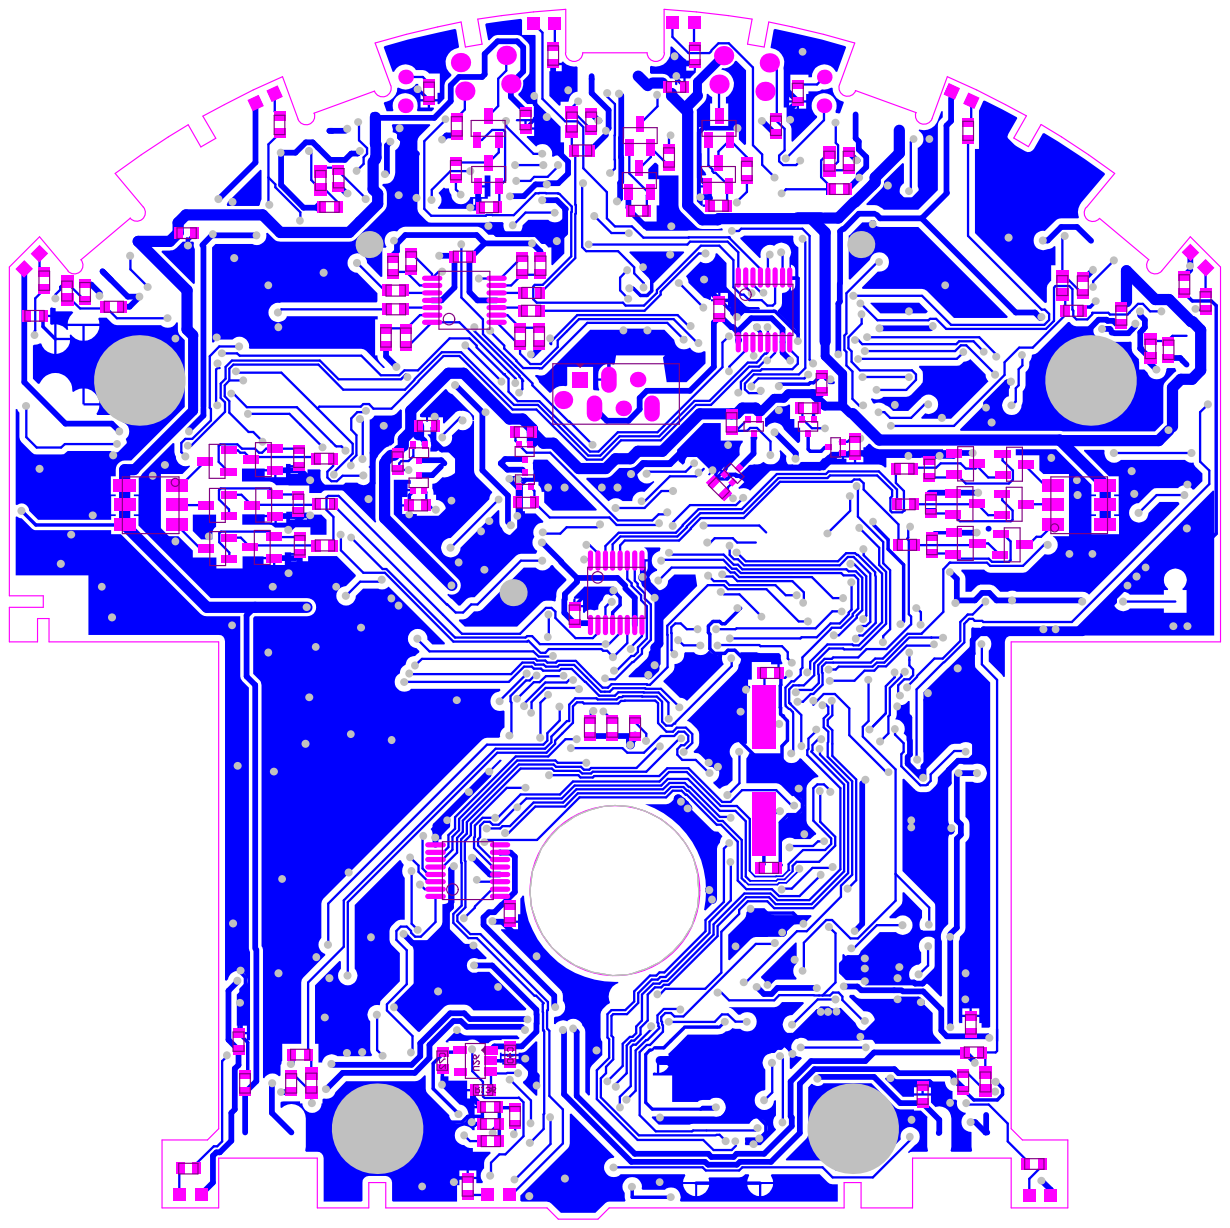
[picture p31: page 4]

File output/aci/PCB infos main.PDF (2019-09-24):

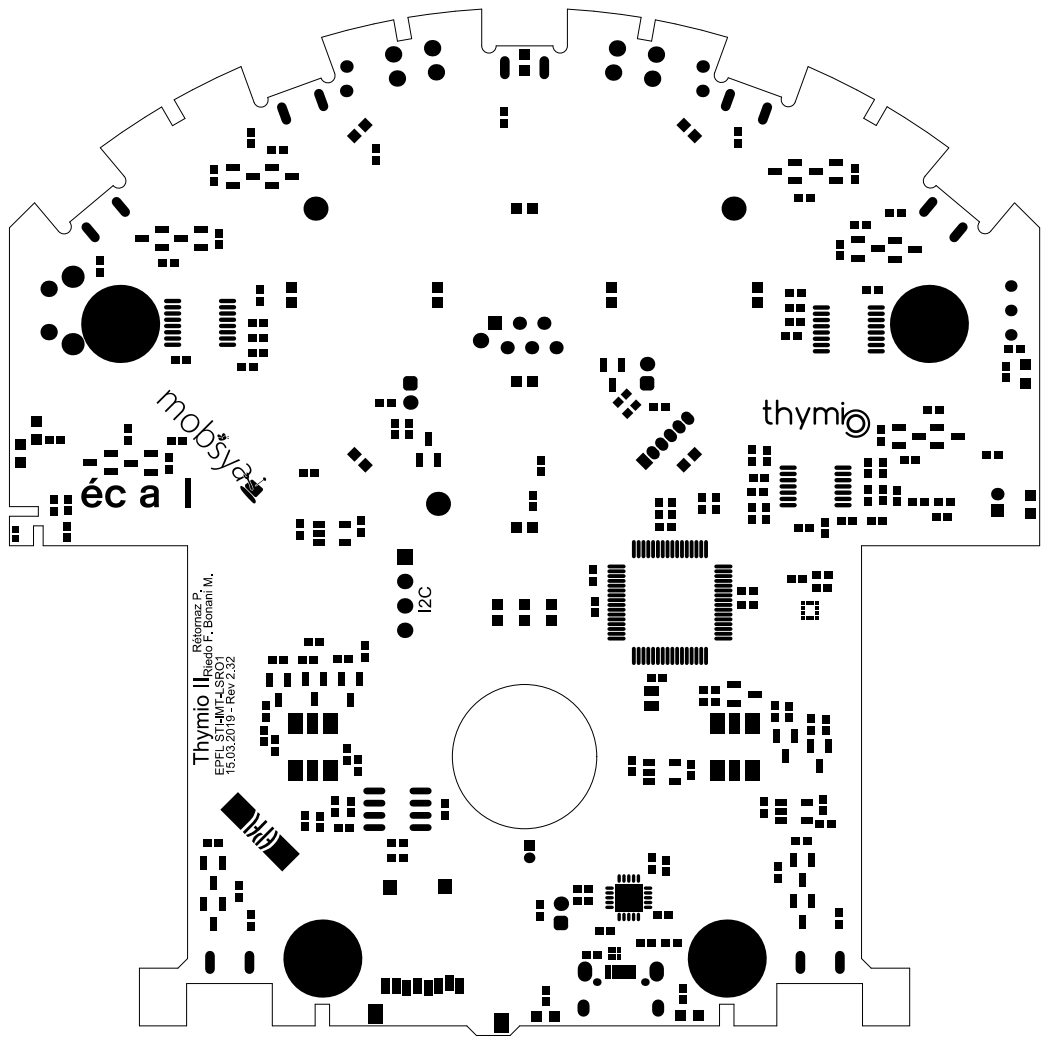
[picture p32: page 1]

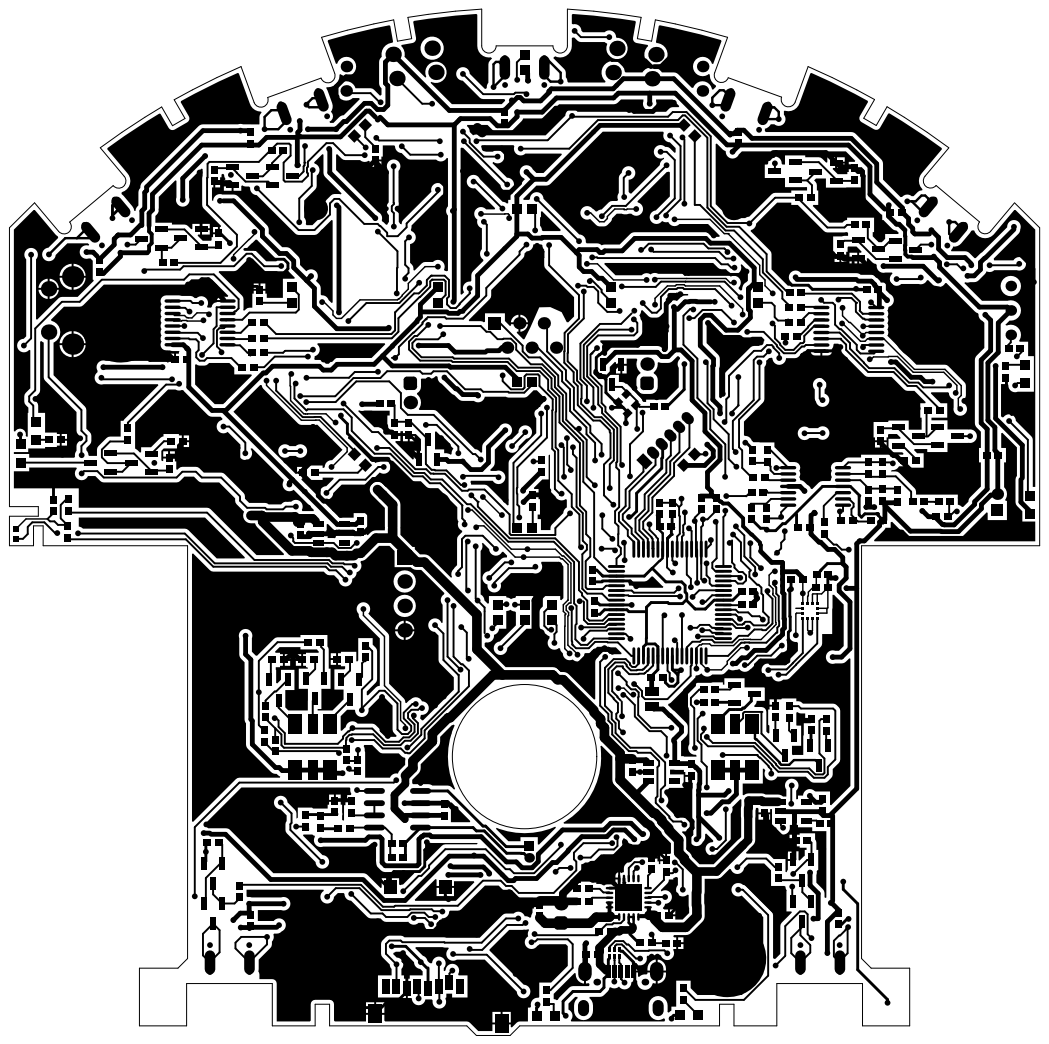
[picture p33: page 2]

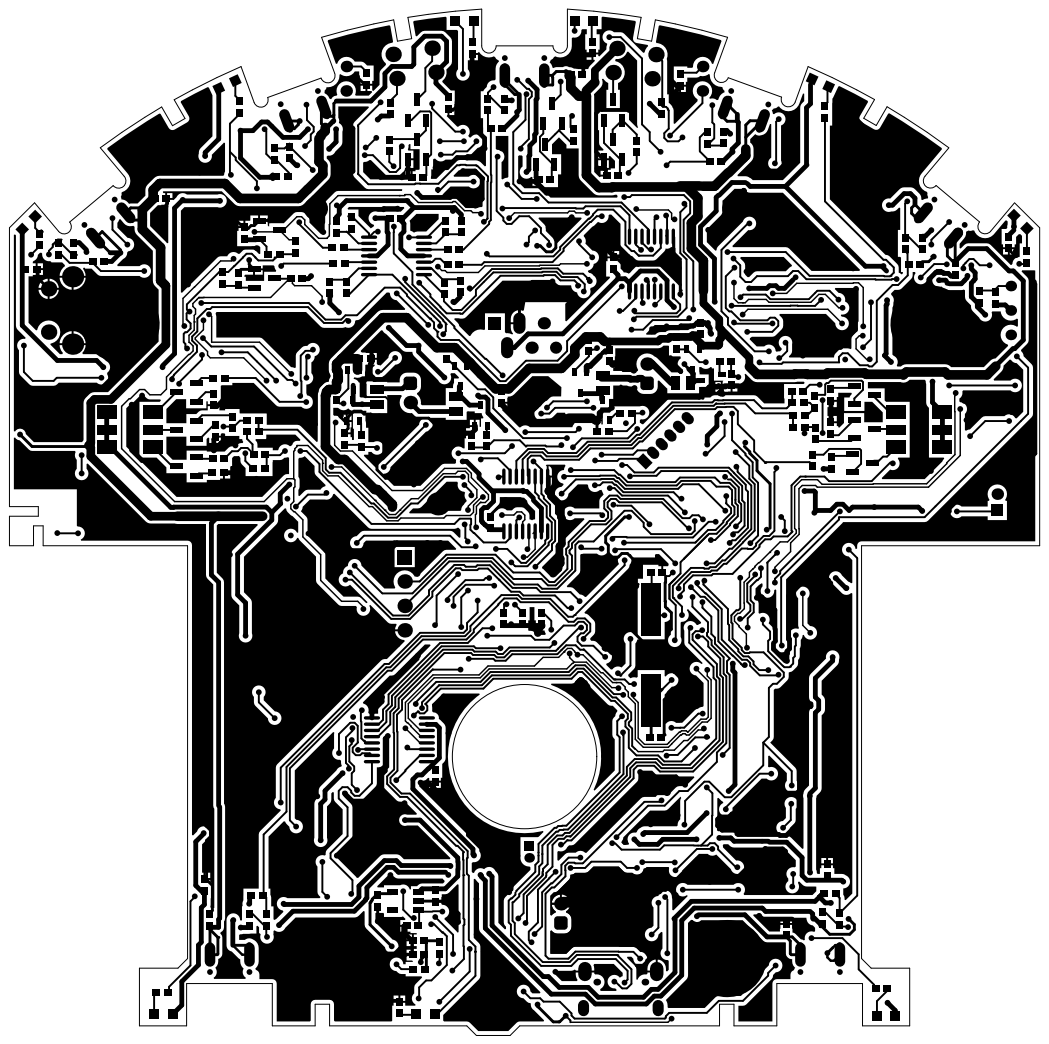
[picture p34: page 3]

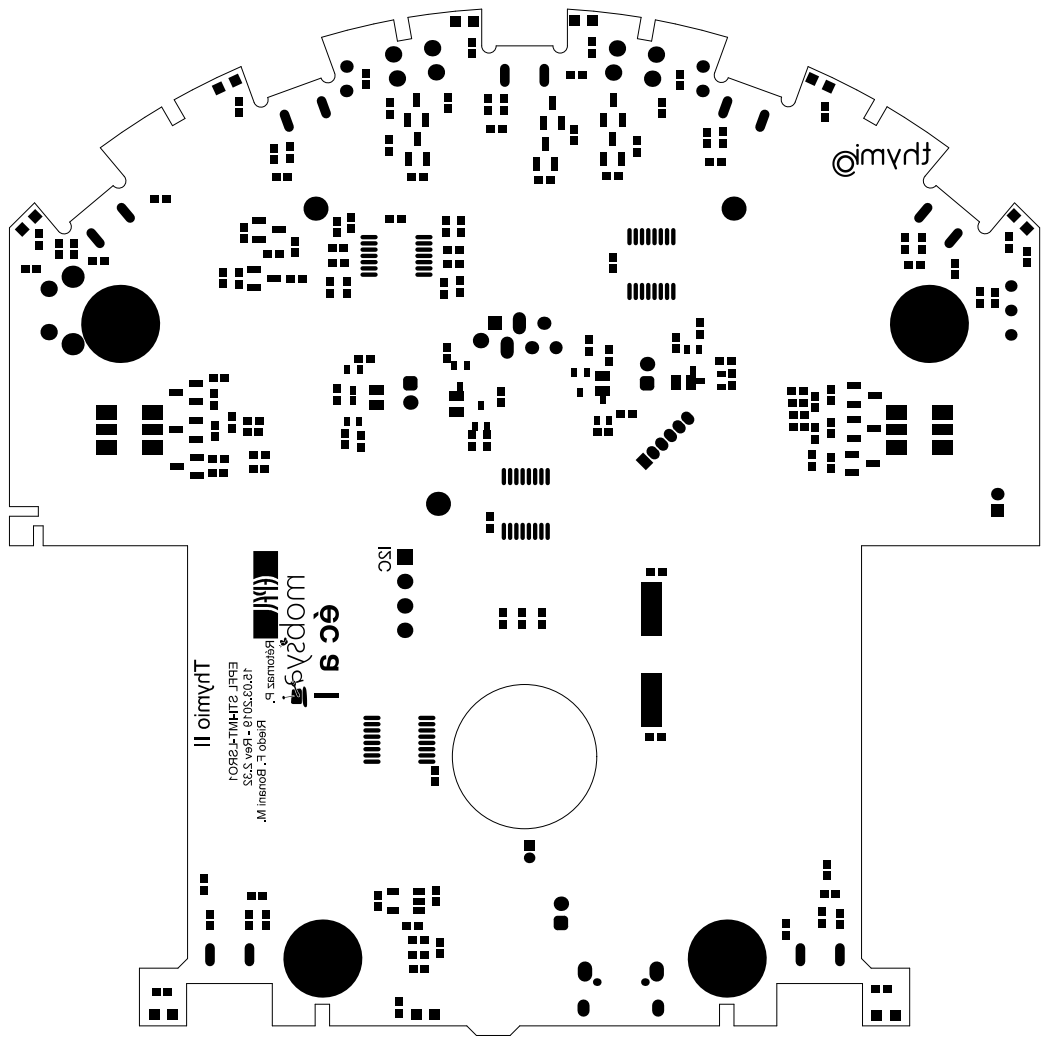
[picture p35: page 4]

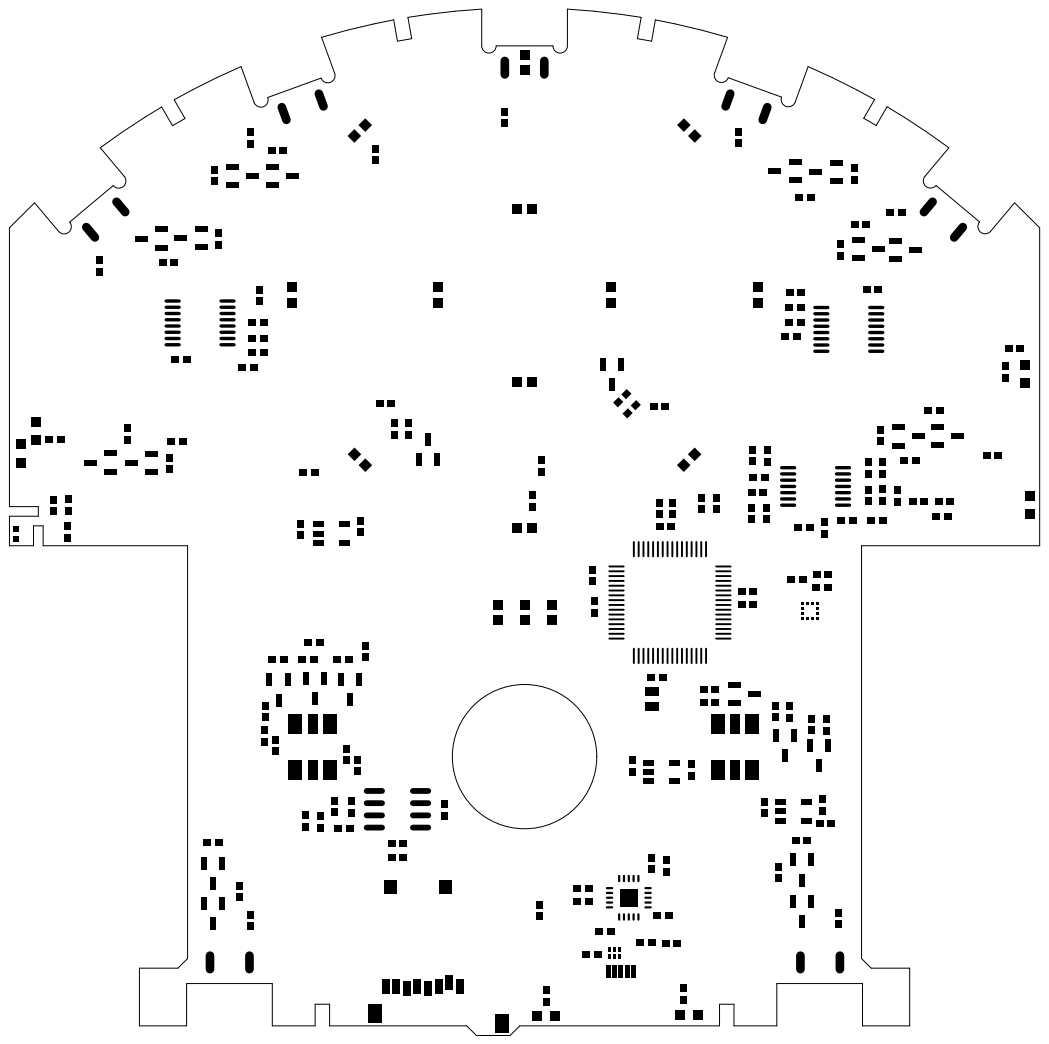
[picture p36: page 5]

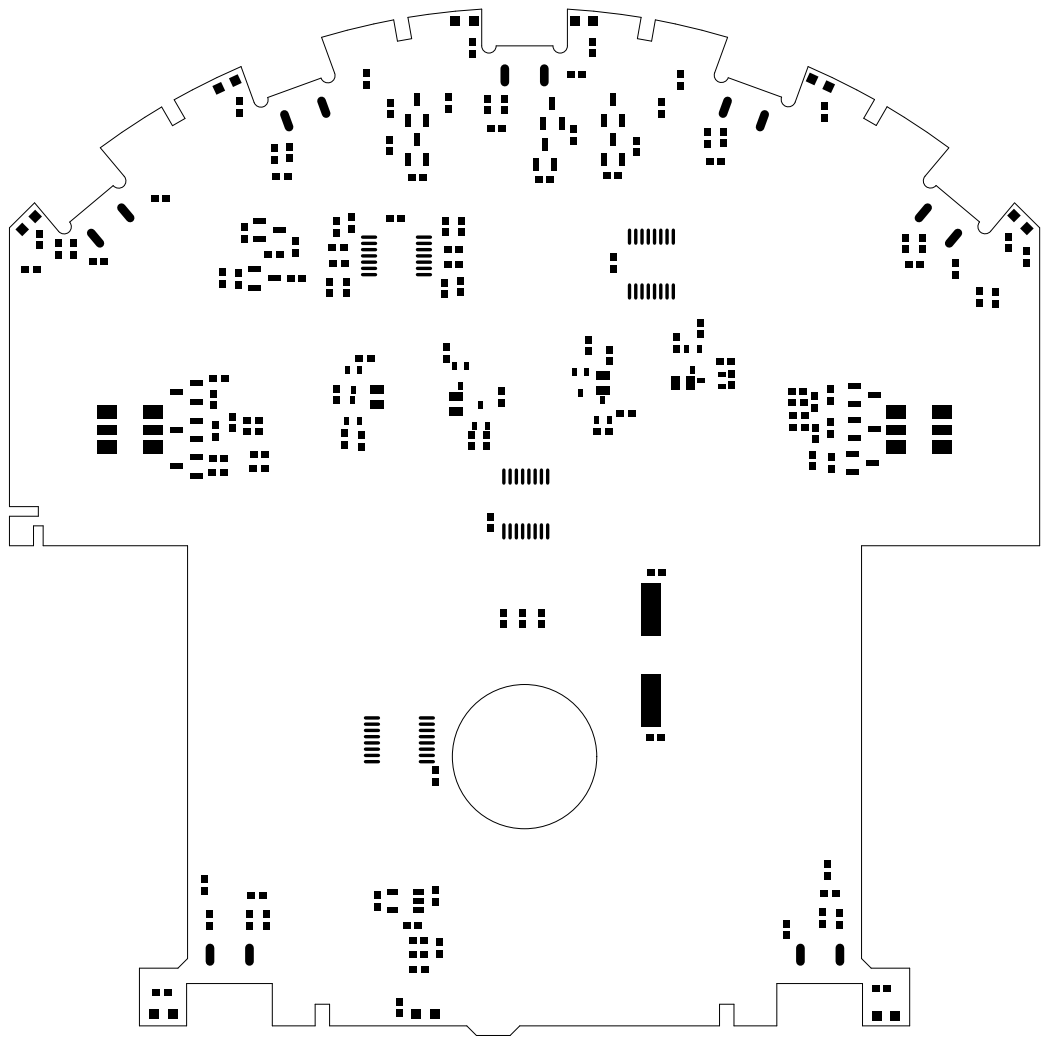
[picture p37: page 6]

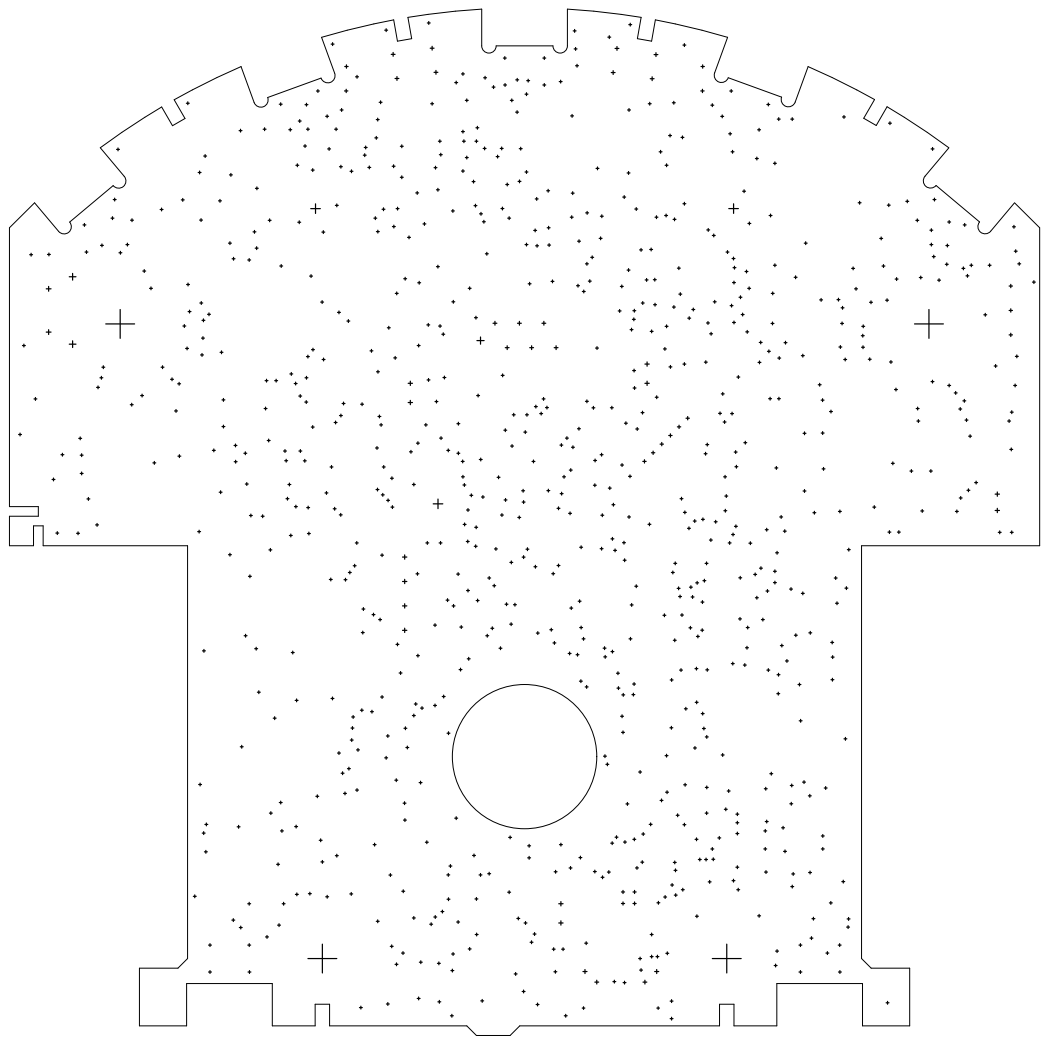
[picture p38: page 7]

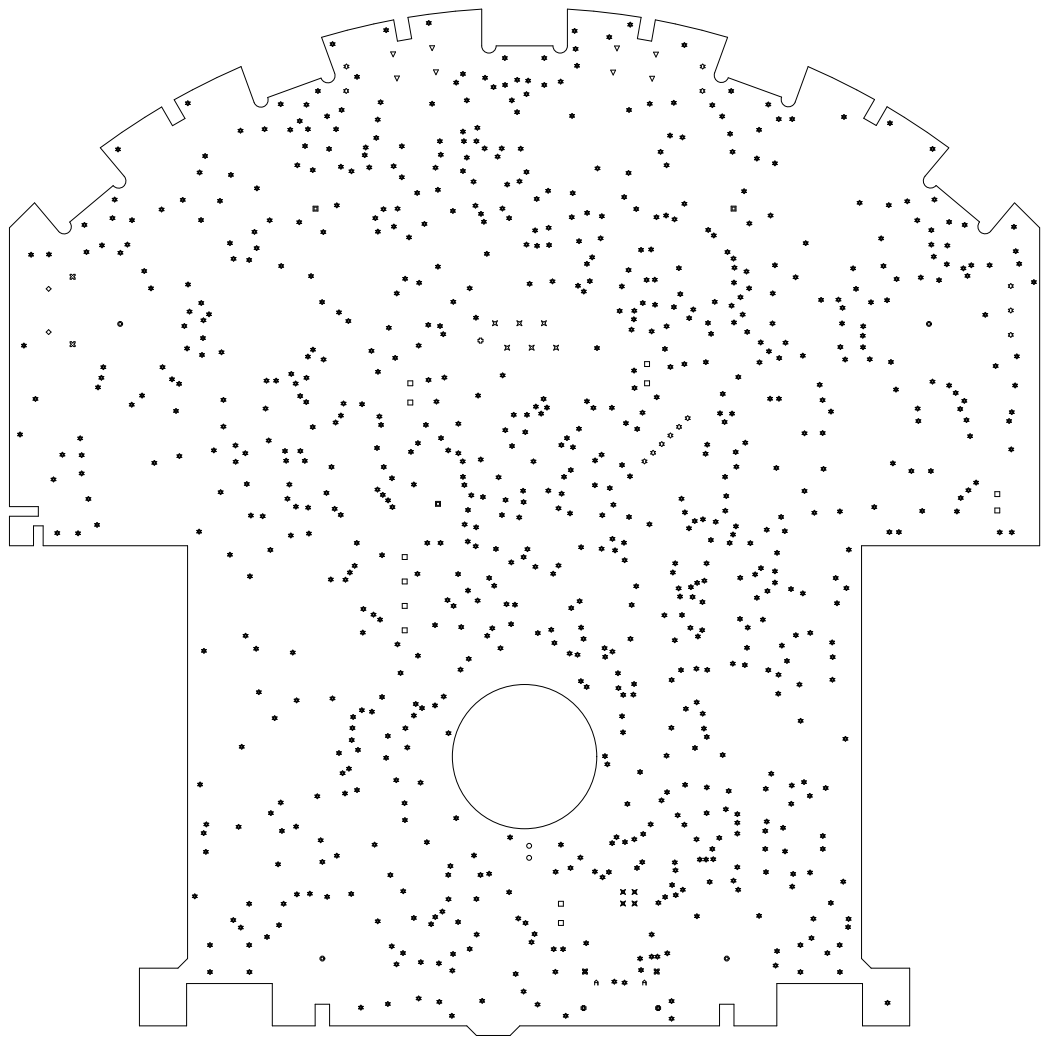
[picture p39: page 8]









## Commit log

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2011-01-20 finish version0.1 pcb pool commande
    [Bill of Materials-thymio2-main.xls, LEDs.SchDoc, USB-power.SchDoc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]
2011-01-21 finish capatouch commande ACI
    [Bill of Materials-thymio2-main.xls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]
2011-01-21 capa touch + adapt value for command
    [IR-sensors.SchDoc, USB-power.SchDoc, sound.SchDoc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]
2011-02-04 Mise à jour pour plan d'implantation
    [Bill of Materials-thymio2-main.xls, IR-sensors.SchDoc, LEDs.SchDoc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]
2011-02-14 version 0.9 en prod
    [IR-sensors.SchDoc, LEDs.SchDoc, microcontroleur.SchDoc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]
2011-02-24 Version 1.0 beta finished, some detailed to control
    [Bill of Materials-thymio2-main.xls, LEDs.SchDoc, SDcard.SchDoc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]
2011-02-27 version 1.0 beta, sent to prod at PCB pool
    [sound.SchDoc, thymio2 capa touch round.PcbDoc]
2011-02-28 version 1.0 beta, clean mounting schematics update shematics resistance value and clean BOM
    [Bill of Materials-thymio2-main.xls, IR-sensors.SchDoc, LEDs.SchDoc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]
2011-03-09 version 1.0 send to china
    [thymio2 capa touch round.GBL, thymio2 capa touch round.GBS, thymio2 capa touch round.GM1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]
2011-03-10 variant pour premier prod en chine
    [Bill of Materials by layers-thymio2-main(Variant of thymio2-main).xls, Bill of Materials-thymio2-main(Variant of thymio2-main).xls, Bill of Materials-thymio2-m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]
2011-03-22 final change for production china
    [Bill of Materials by layers-thymio2-main(Variant of thymio2-main).xls, Bill of Materials-thymio2-main(Variant of thymio2-main).xls, IR-sensors.SchDoc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]
2011-03-22 add 10k pull down to VA enable
    [Bill of Materials by layers-thymio2-main(Variant of thymio2-main).xls, Bill of Materials-thymio2-main(Variant of thymio2-main).xls, USB-power.SchDoc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]
2011-03-29 version 1.1 with 0.5mm clearance between composant
    [thymio2-main.DRL, thymio2-main.GBL, thymio2-main.GBP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]
2011-04-04 prod final chine version 1.1
    [thymio2-main.DRL, thymio2-main.GBL, thymio2-main.GBP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]
2011-10-20 version 1.2 manufacture for testing increase routing change routing of spi elarge space for sensors better routing of motor power
    [LEDs.SchDoc, SDcard.SchDoc, sound.SchDoc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]
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2012-01-17 version 1.4 for 2 production change accelerometer and microphone footprint bigger hole for motor cable
    [sound.SchDoc, thymio2 capa touch round.PcbDoc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]
2012-08-14 version 1.5 production 02.04.12
    [LEDs.SchDoc, sound.SchDoc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]
2012-08-14 small change new version
    [thymio2-main.PrjPCB]
2012-09-04 add self for motor, unified footprints capa resistor
    [Bill of Materials by layers-thymio2-main(Production Thymio2).xlsx, Bill of Materials-thymio2-main(Production Thymio2).xlsx, IR-sensors.SchDoc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]
2012-09-10 output version 1.61 send to ACI with new connector for motors and battery
    [Bill of Materials by layers-thymio2-main(Production Thymio2).xlsx, Bill of Materials-thymio2-main(Production Thymio2).xlsx, USB-power.SchDoc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]
2012-12-14 version 1.63 in production for 2013 adapt IR sensor footprint to for more reliability
    [Bill of Materials by layers-thymio2-main(Production Thymio2).xlsx, Bill of Materials-thymio2-main(Production Thymio2).xlsx, IR-sensors.SchDoc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]
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2014-03-25 new production version 1.71 add control of output enable of led drivers to fix power on problems when the Battery is connected
    [Bill of Materials by layers-thymio2-main(Production Thymio2).xlsx, Bill of Materials-thymio2-main(Production Thymio2).xlsx, LEDs.SchDoc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]
2014-03-28 change usb connector footprint version 1.7.2 final for production 2014
    [Bill of Materials by layers-thymio2-main(Production Thymio2).xlsx, Bill of Materials-thymio2-main(Production Thymio2).xlsx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]
2014-07-23 project update altium version
    [thymio2-main.PrjPCB]
2017-08-15 clean project and rename 3d Models path
    [a_thymio_2_asm.stp, batt_103048_prt.stp, delta_pt-20-8_prt.stp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]
2017-08-22 change USB connector and upgrade version
    [USB-power.SchDoc, thymio2-main.PrjPCB]
2017-11-21 add led protection for short circuit and adapt value for IEC 60825
    [LEDs.SchDoc, thymio2-main.PrjPCB]
2017-11-23 change cartouche and generate output files
    [IR-sensors.SchDoc, LEDs.SchDoc, SDcard.SchDoc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]
2017-12-14 small change on USB connector and create output
    [thymio2-main.GBL, thymio2-main.GBO, thymio2-main.GBP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]
2018-02-06 change RGB led, switch red and green according new led to keep comparability, upgrade version
    [LEDs.SchDoc, thymio2-main.PcbLib, thymio2-main.PrjPCB]
2018-02-09 small cleaning and generate production file
    [Bill of Materials by layers-thymio2-main(Production Thymio2).xlsx, Bill of Materials-thymio2-main(Production Thymio2).xlsx, LEDs.SchDoc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]
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2018-03-20 add LDO for RGB led and remove current source
    [LEDs.SchDoc, USB-power.SchDoc, microcontroleur.SchDoc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]
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2018-06-01 change resistor led value change shift register outputs 2.01
    [Bill of Materials by layers-thymio2-main(Production Thymio2).xlsx, Bill of Materials-thymio2-main(Production Thymio2).xlsx, LEDs.SchDoc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]
2018-07-04 change 3.3uF self to EMI 600Ohm inductance Chip Beads
    [IR-sensors.SchDoc, LEDs.SchDoc, SDcard.SchDoc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]
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2018-12-14 change resistor and capacitor from 0603 to 0402 in schematics
    [IR-sensors.SchDoc, LEDs.SchDoc, SDcard.SchDoc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]
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2018-12-17 replace MOSFET by bigger one
    [motor.SchDoc, thymio2-main.PcbLib]
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2019-02-20 change ldo and create output file for certification
    [IR-sensors.SchDoc, LEDs.SchDoc, SDcard.SchDoc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]
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2019-03-01 add zero ohm resistor to choose different leds, generates outputs
    [Bill of Materials by layers-thymio2-main(Production Thymio2_for_testing).xls, Bill of Materials-thymio2-main(Production Thymio2_for_testing).xls, LEDs.SchDoc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]
2019-05-01 fix some routing for production and generate outputs
    [thymio2-main.PrjPCB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]
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
